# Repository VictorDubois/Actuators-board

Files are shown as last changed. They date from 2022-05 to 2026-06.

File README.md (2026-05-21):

Compact ESP32-based PCB, to control:
- 2 steppers
- 8 hobby servomotors (dedicated 6V DC-DC)
- AX12 Dynamixel numeric servomotors
- Addressable LEDs
- 2 vaccum sensors
- 4 generic GPIO connectors
- 3 generic I2C connectors
- 2 Krabi-Bus (12V/12V power/24V power/CAN)

[The code is available here](https://github.com/VictorDubois/ActuatorBoardCode)

[Click for online viewer
Capture d’écran du 2026-05-21 20-24-05
Capture d’écran du 2026-05-21 20-24-27
](https://kicanvas.org/?repo=https%3A%2F%2Fgithub.com%2FVictorDubois%2FActuators-board)

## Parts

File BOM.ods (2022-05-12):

> C1, C2 | 100nF | Capacitor_SMD:C_0805_2012Metric | ~ | 2 | 1.38
C4 | C | Capacitor_SMD:C_0805_2012Metric | ~ | 1 | 1.38
D1 | 13V | Diode_SMD:D_1206_3216Metric | ~ | 1 | 1.41
> D2, D3, D5, D30 | D_Zener | Diode_SMD:D_1206_3216Metric | ~ | 4 | 2/3 => 1.55 | D5/30 =>1,46
> D4, D6, D7, D25, D26, D31 | D | Diode_SMD:D_1206_3216Metric | ~ | 6 | 1.42
> D8-D24, D32, D33 | D_Zener_Small | Diode_SMD:D_1206_3216Metric | ~ | 19 | 1.39
> D27-D29 | LED_Small | LED_SMD:LED_0805_2012Metric | ~ | 3 | TOP
> Q1-Q4 | DMN2011UTS | Package_SO:TSSOP-8_4.4x3mm_P0.65mm | https://docs.rs-online.com/3df4/0900766b816b6b93.pdf | 4 | 1.44
> Q5, Q6 | DMP2040USD | Package_SO:SO-8_3.9x4.9mm_P1.27mm | https://docs.rs-online.com/a60c/0900766b816b6bbd.pdf | 2 | 1.43
> R1, R6 | 22kR | Resistor_SMD:R_0603_1608Metric | ~ | 2 | 1.54
R8 | 680R | Resistor_SMD:R_0603_1608Metric | ~ | 1 | 1.52
> R2-R5, R7, R9, R17-R20 | 220R | Resistor_SMD:R_0603_1608Metric | ~ | 10 | 1.40 | R2/R7 => 1.47 (2.2k)
R11 | open | Resistor_SMD:R_0603_1608Metric | ~ | 1
> R10, R12 | 0R | Resistor_SMD:R_0603_1608Metric | ~ | 2 | 1.45
> U1, U2 | XGZP6897D_differential_pressure_sensor | LibraryVictor:SOIC-8_7.5x5.85mm_P1.27mm |  | 2

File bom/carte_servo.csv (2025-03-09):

Reference | Value | LCSC# | Qty | Footprint | Datasheet | DNP
C1,C2,C7,C8,C10,C12,C23,C28,C29,C35 | 100nF | C14663 | 10 | Capacitor_SMD:C_0603_1608Metric | -- mixed values --
C3,C26,C27 | C_Polarized | C398835 | 3 | Capacitor_THT:CP_Radial_D10.0mm_P5.00mm | ~
C4,C9,C19,C20,C21,C22,C31,C32 | 10uF | C1713 | 8 | Capacitor_SMD:C_0805_2012Metric | ~
C5 | 1µF | C15849 | 1 | Capacitor_SMD:C_0603_1608Metric | ~
C6,C11 | 4.7µF | C1705 | 2 | Capacitor_SMD:C_0603_1608Metric | ~
C13 | 2.2uF | C19110 | 1 | Capacitor_SMD:C_0805_2012Metric | ~
C14 | 470nF | C7503496 | 1 | Capacitor_SMD:C_0603_1608Metric | ~
C15 | 68pF | C62782 | 1 | Capacitor_SMD:C_0603_1608Metric | ~
C16,C17,C30 | 47uF | C5440143 | 3 | Capacitor_SMD:C_1210_3225Metric | ~
C18 | 10nF | C57112 | 1 | Capacitor_SMD:C_0603_1608Metric | ~
C24,C25 | 22uF | C5674 | 2 | LED_SMD:LED_0805_2012Metric | ~
C33 | 470µF | C106619 | 1 | Capacitor_THT:CP_Radial_D7.5mm_P2.50mm | ~
C34 | C_Small | ? | 1 | Capacitor_SMD:C_0805_2012Metric | ~
D1,D8 | 13V | C173428 | 2 | Diode_SMD:D_SOD-123 | ~
D2,D3 | ESD321 | C3008120 | 2 | Diode_SMD:D_SOD-523 | https://www.mouser.fr/ProductDetail/Texas-Instruments/ESD321DYAR?qs=rQFj71Wb1eXoYwRMra0IYA%3D%3D
D4,D27 | LED_G | C965815 | 2 | LED_SMD:LED_0805_2012Metric | ~
D5,D6,D7,D13,D21,D22,D23,D24,D25,D26,D30,D32,D33,D34,D35,D36,D37,D38,D41,D48 | D_Zener_Small | C908230 | 20 | Diode_SMD:D_SOD-123 | ~
D29 | LED_R | C965812 | 1 | LED_SMD:LED_0805_2012Metric | ~
F1,F2 | Fuse 4A | C27515 | 2 | Fuse:Fuse_Littelfuse-NANO2-451_453 | ~
J1,J3 | Conn_01x04_Pin | C595709 | 2 | Connector_JST:JST_XH_B4B-XH-A_1x04_P2.50mm_Vertical | Stepper
J2,J22 | Conn_02x04_Top_Bottom | C277661 | 2 | Connector_Molex:Molex_Micro-Fit_3.0_43045-0812_2x04_P3.00mm_Vertical | ~
J4,J26,J27,J28 | Conn_01x03 | C144394 | 4 | Connector_JST:JST_XH_B3B-XH-A_1x03_P2.50mm_Vertical | ~
J5,J6,J7,J8,J9,J10,J18,J19 | Conn_01x03_Male | C2937625 | 8 | Connector_PinHeader_2.54mm:PinHeader_1x03_P2.54mm_Vertical | ~
J11 | Transistor_2 | C158012 | 1 | Connector_JST:JST_XH_B2B-XH-A_1x02_P2.50mm_Vertical | ~
J12 | Transistor_1 | C158012 | 1 | Connector_JST:JST_XH_B2B-XH-A_1x02_P2.50mm_Vertical | ~
J13 | Transistor_4 | C158012 | 1 | Connector_JST:JST_XH_B2B-XH-A_1x02_P2.50mm_Vertical | ~
J14 | Transistor_.3 | C158012 | 1 | Connector_JST:JST_XH_B2B-XH-A_1x02_P2.50mm_Vertical | ~
J16,J17,J23 | Conn_01x05 | C495550 | 3 | Connector_JST:JST_XH_B5B-XH-A_1x05_P2.50mm_Vertical | ~
J24 | Conn_LEDs | C144394 | 1 | Connector_JST:JST_XH_B3B-XH-A_1x03_P2.50mm_Vertical | ~
J25,J29 | Conn_AX12 | C144394 | 2 | Connector_JST:JST_XH_B3B-XH-A_1x03_P2.50mm_Vertical | ~
L1 | XAL6030-122MEC | C19191689 | 1 | XAL6030-122MEC:IND_XAL6030-122MEC | https://www.mouser.fr/ProductDetail/Coilcraft/XAL6030-122MEC?qs=zCSbvcPd3pa9JIn1HYfyrA%3D%3D
L2 | IHLP2525CZER3R3M11 | C845025 | 1 | INDPM6965X300N | https://datasheet.datasheetarchive.com/originals/distributors/Datasheets-DGA11/2253392.pdf
P1 | USB_C_Plug_USB2.0 | C963216 | 1 | USBC:G-Switch GT-USB-7047A | https://www.lcsc.com/product-detail/USB-Connectors_G-Switch-GT-USB-7047A_C963216.html
Q1,Q2,Q3,Q4,Q6 | DMN2011UTS | C5245271 | 5 | Package_SO:TSSOP-8_4.4x3mm_P0.65mm | https://docs.rs-online.com/3df4/0900766b816b6b93.pdf
Q7 | CSD17307Q5A | C22367097 | 1 | Package_TO_SOT_SMD:TDSON-8-1 | http://www.ti.com/lit/gpn/csd17307q5a
Q8 | CSD17579Q5A | C2760461 | 1 | Package_TO_SOT_SMD:TDSON-8-1 | http://www.ti.com/lit/gpn/csd17579q5a
R1 | 1.74k | C2930053 | 1 | Capacitor_SMD:C_0603_1608Metric | ~
R2,R17,R18,R19,R20 | 220R | C2907127 | 5 | Resistor_SMD:R_0603_1608Metric | ~
R3,R4 | 2kR | C2907137 | 2 | Resistor_SMD:R_0603_1608Metric | ~
R5,R27,R29 | 5.11kR | C2933233 | 3 | Resistor_SMD:R_0603_1608Metric | ~
R6,R7,R12,R13,R14 | NC |  | 5 | Resistor_SMD:R_0603_1608Metric | ~
R8,R31 | 52.3kR | C23198 | 2 | Resistor_SMD:R_0603_1608Metric | ~
R9,R22,R23,R24,R26,R35,R36 | 10kR | C2930027 | 7 | Resistor_SMD:R_0603_1608Metric | ~
R10,R11,R15,R16,R37 | 0R | C21189 | 5 | Resistor_SMD:R_0603_1608Metric | ~
R21 | 510R | C2907179 | 1 | Resistor_SMD:R_0805_2012Metric | ~
R25,R30 | 22kR | C2907128 | 2 | Resistor_SMD:R_0603_1608Metric | ~
R28 | 1MR | C22935 | 1 | Resistor_SMD:R_0603_1608Metric | ~
R32 | 88.7k | C2999456 | 1 | Capacitor_SMD:C_0603_1608Metric | ~
R33 | 9.76k | C2933269 | 1 | Capacitor_SMD:C_0603_1608Metric | ~
R34 | 56.2k | C2930117 | 1 | Capacitor_SMD:C_0603_1608Metric | ~
R38,R39 | 1kR | C2907113 | 2 | Resistor_SMD:R_0603_1608Metric | ~
R40,R41,R42,R43,R44,R45,R46,R47 | R_Small |  | 8 | Resistor_SMD:R_0603_1608Metric | ~
SW2 | SW_Push | C2888419 | 1 | button:BZCN TSA007A1518B03 | https://www.lcsc.com/product-detail/Tactile-Switches_BZCN-TSA007A1518B03_C2888419.html
U1,U2 | XGZP6897D_differential_pressure_sensor |  | 2 | LibraryVictor:SOIC-8_7.5x5.85mm_P1.27mm
U3,U4 | TMC2208_SILENTSTEPSTICK |  | 2 | TMC2208_SILENTSTEPSTICK:MODULE_TMC2208_SILENTSTEPSTICK
U5 | 74LVC2G241 | C10430 | 1 | Package_SO:VSSOP-8_2.4x2.1mm_P0.5mm | http://www.ti.com/lit/sg/scyt129e/scyt129e.pdf
U6 | SN65HVD230 | C12084 | 1 | Package_SO:SOIC-8_3.9x4.9mm_P1.27mm | http://www.ti.com/lit/ds/symlink/sn65hvd230.pdf
U7 | LD1117S33TR_SOT223 | C20538890 | 1 | Package_TO_SOT_SMD:SOT-223-3_TabPin2 | http://www.st.com/st-web-ui/static/active/en/resource/technical/document/datasheet/CD00000544.pdf
U8 | ESP32-S3-WROOM-1 | C2913198 | 1 | PCM_Espressif:ESP32-S3-WROOM-1U | https://www.espressif.com/sites/default/files/documentation/esp32-s3-wroom-1_wroom-1u_datasheet_en.pdf
U9 | LM3150MH | C1519420 | 1 | Package_SO:HTSSOP-14-1EP_4.4x5mm_P0.65mm_EP3.4x5mm_Mask3x3.1mm | http://www.ti.com/lit/ds/symlink/lm3150.pdf
U10 | TPS563200 | C97253 | 1 | Package_TO_SOT_SMD:SOT-23-6 | http://www.ti.com/lit/ds/symlink/tps563200.pdf
U11 | PCF8574ATS | C2803277 | 1 | Package_SO:SSOP-20_4.4x6.5mm_P0.65mm | http://www.nxp.com/docs/en/data-sheet/PCF8574_PCF8574A.pdf

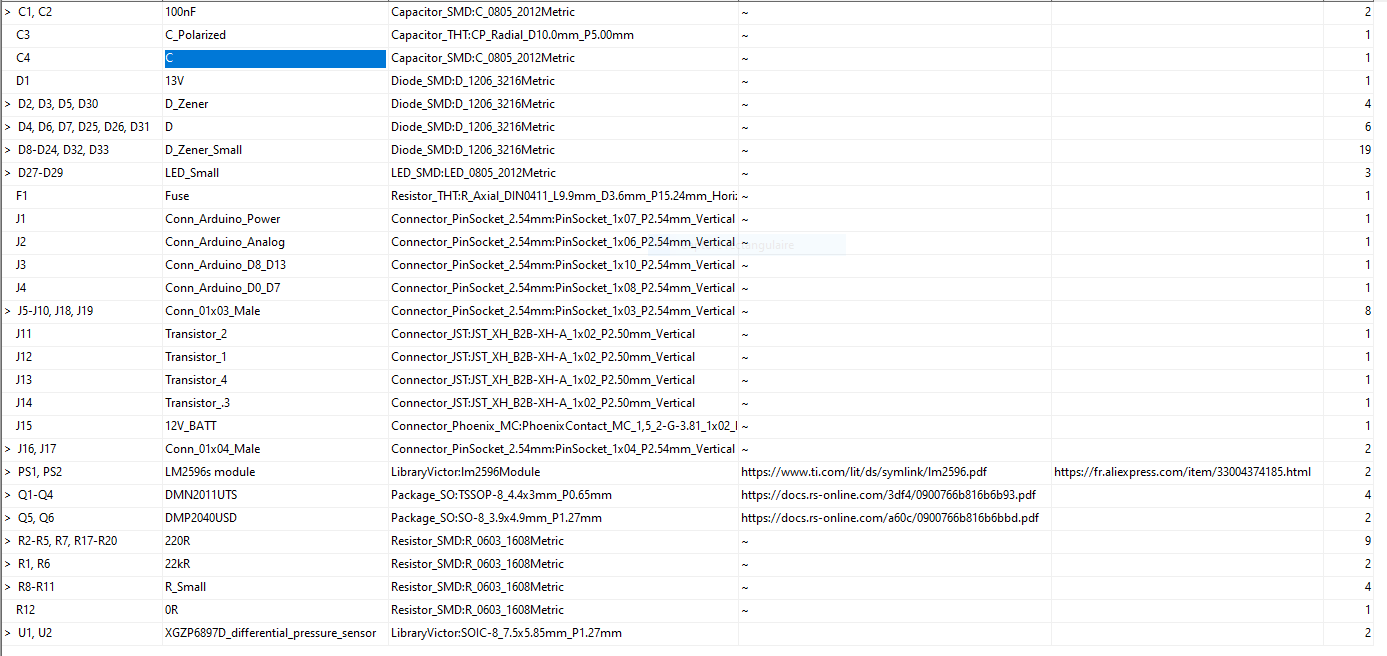
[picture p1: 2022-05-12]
BOM.PNG

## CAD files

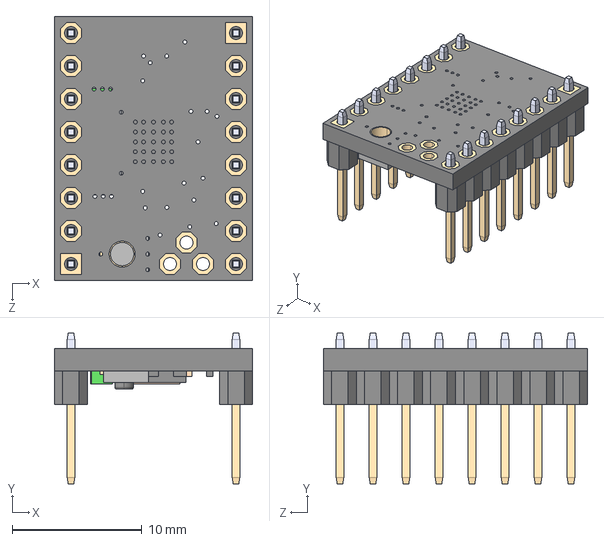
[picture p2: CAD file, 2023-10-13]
TMC2208_SILENTSTEPSTICK/TMC2208_SILENTSTEPSTICK.step
15.2 x 11.6 x 20.3 mm

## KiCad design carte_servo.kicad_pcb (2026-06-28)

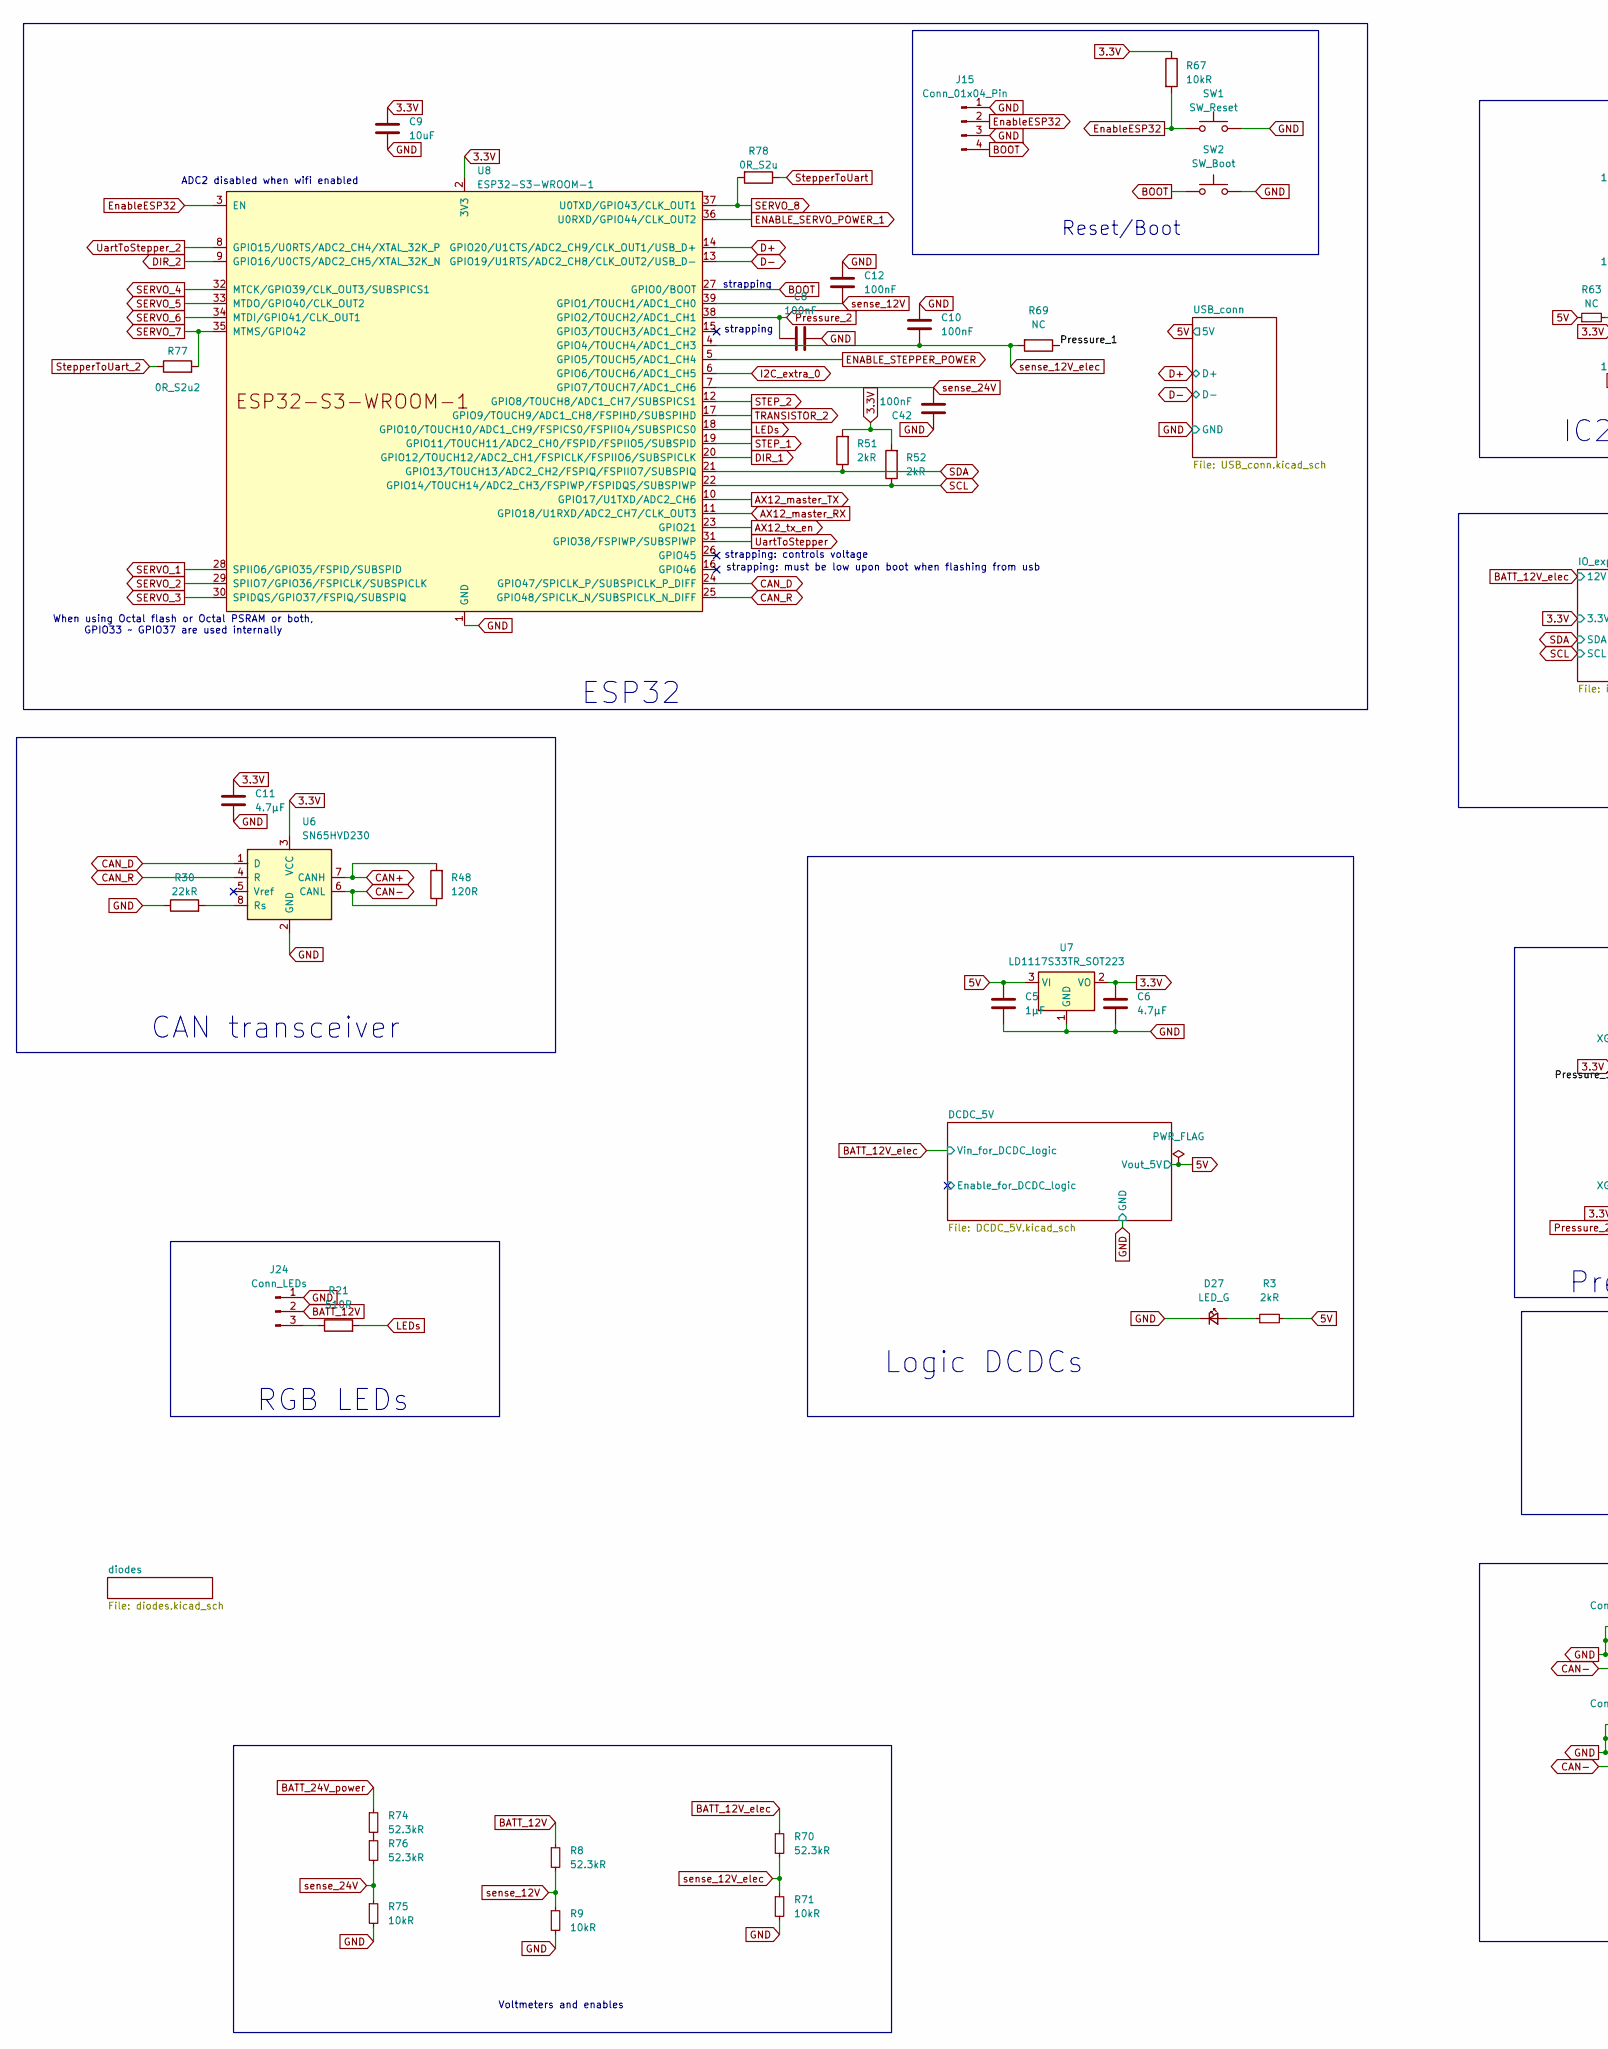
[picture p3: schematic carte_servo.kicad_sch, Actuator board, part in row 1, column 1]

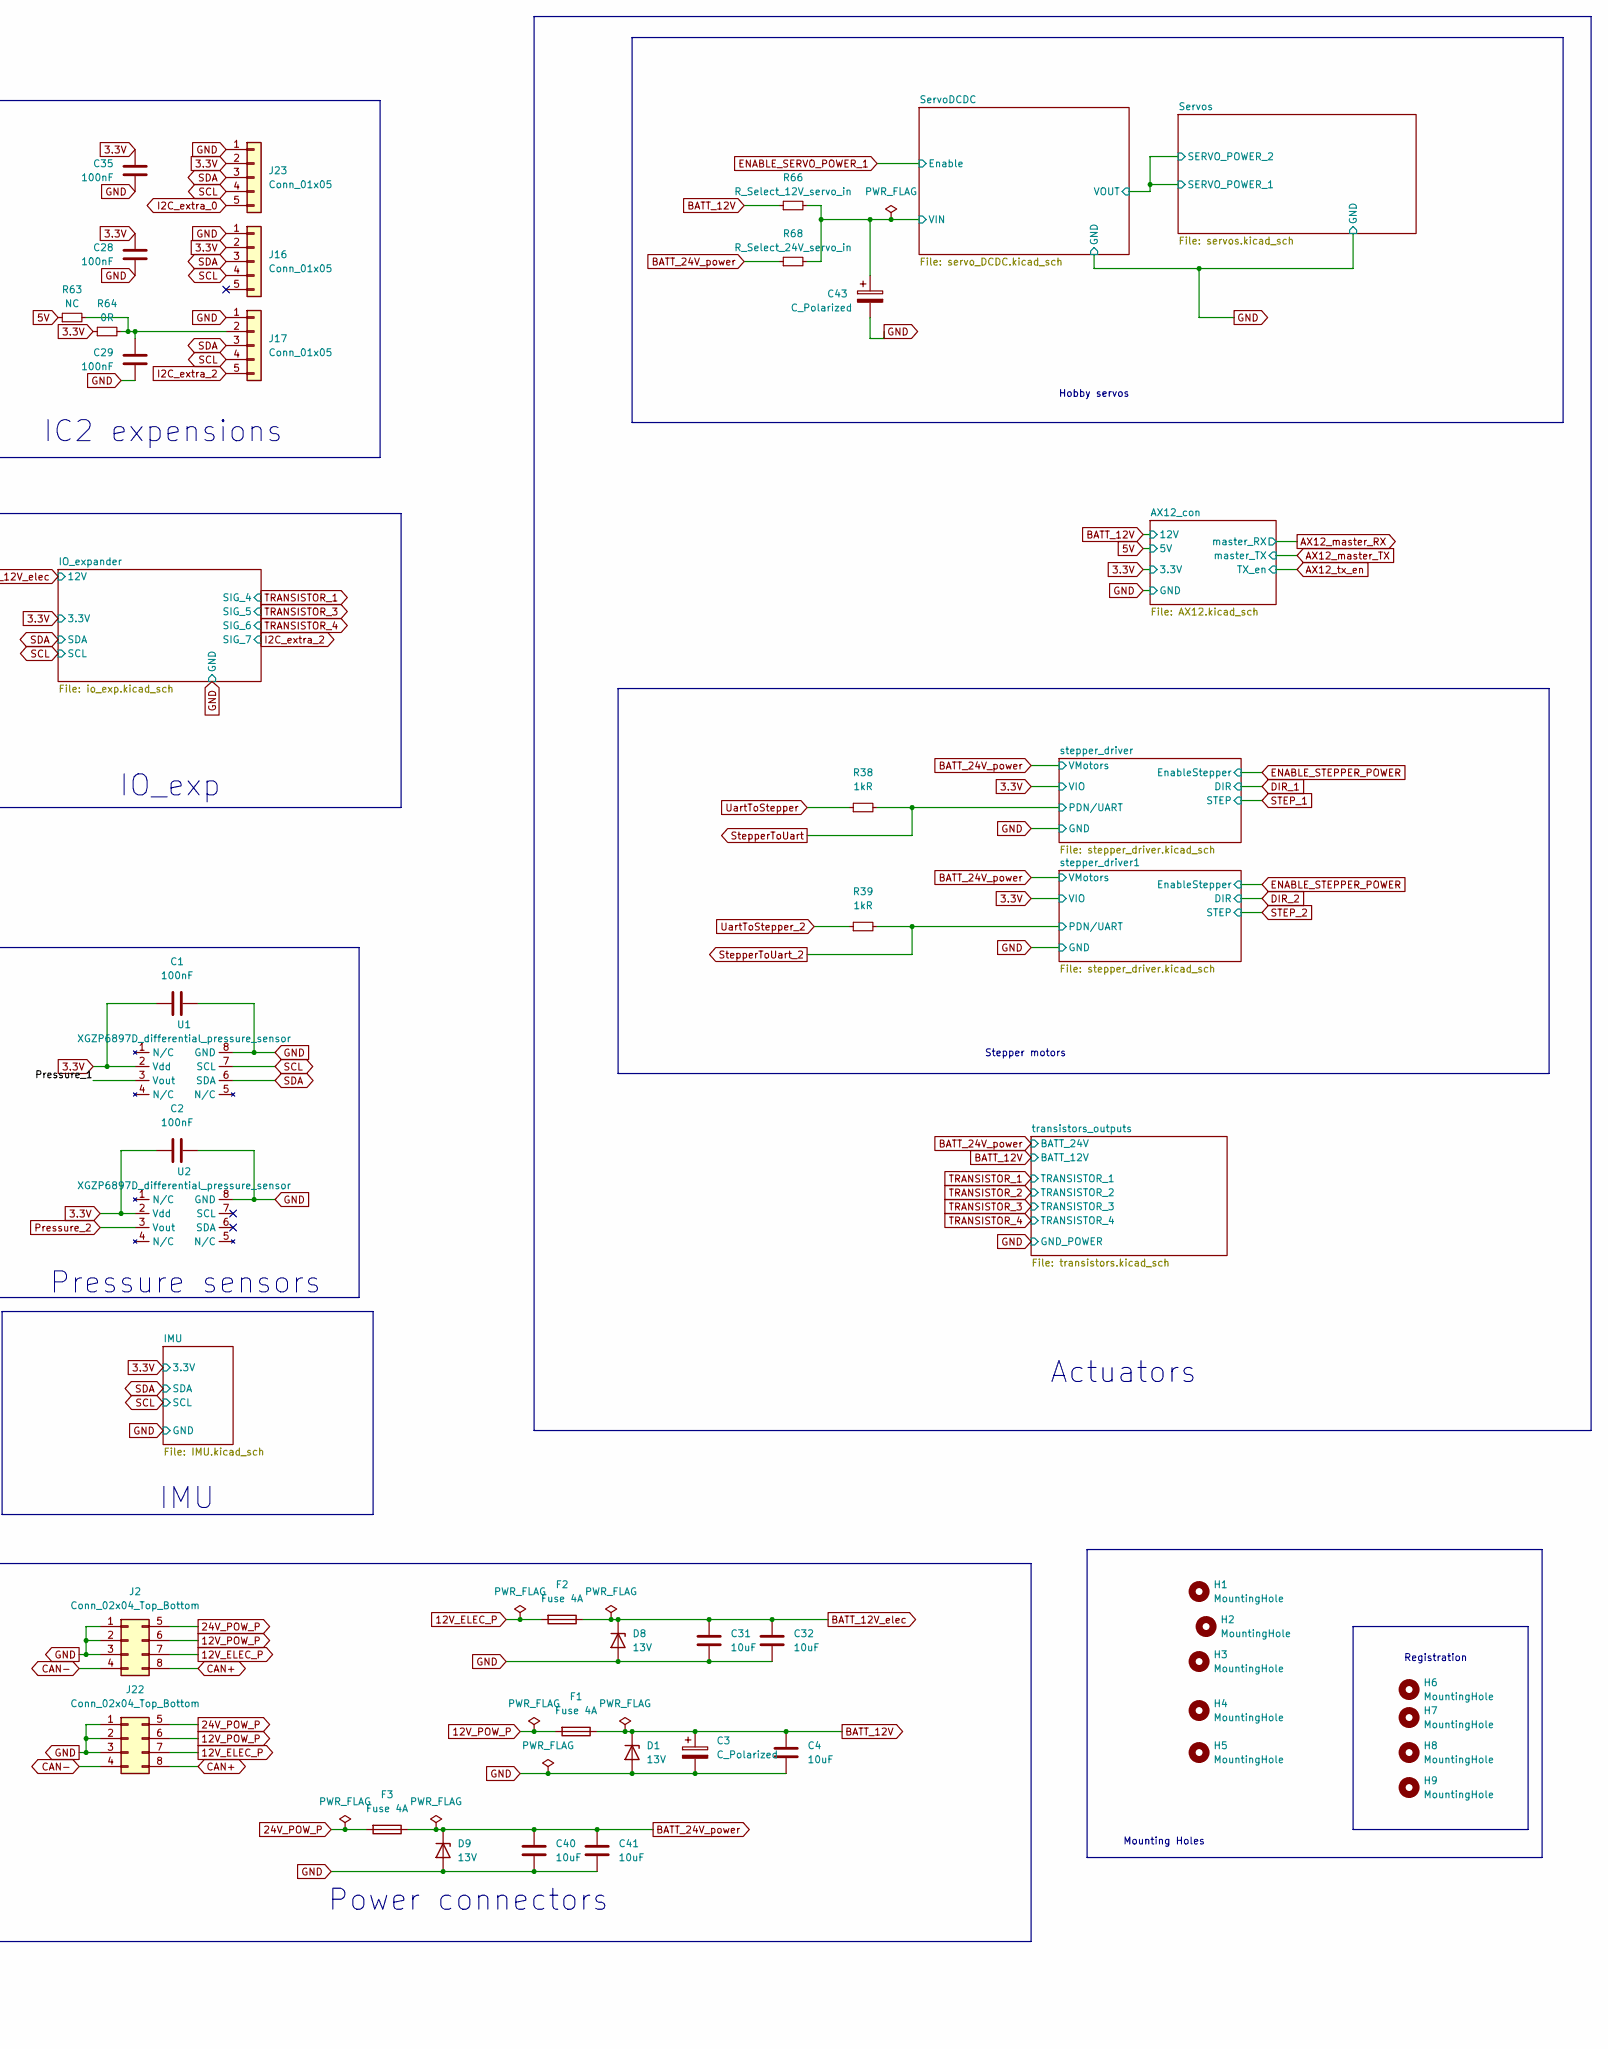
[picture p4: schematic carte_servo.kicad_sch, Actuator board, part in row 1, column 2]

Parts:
C1, C2, C8, C10, C12, C28, C29, C35, C42: 100nF; C_0603_1608Metric; LCSC# C14663
C3: C_Polarized; CP_Radial_D10.0mm_P5.00mm; LCSC# C398835
C4, C9, C31, C32, C40, C41: 10uF; C_0805_2012Metric; LCSC# C440198
C5: 1µF; C_0603_1608Metric; LCSC# C15849
C6, C11: 4.7µF; C_0603_1608Metric; LCSC# C1705
C43: C_Polarized; CP_Elec_10x10.5; LCSC# C233118
D1, D8, D9: 13V; D_SOD-123; LCSC# C173428
D27: LED_G; LED_0805_2012Metric; LCSC# C965815
F1, F2, F3: Fuse 4A; Fuse_Littelfuse-NANO2-451_453; LCSC# C27515
H1, H2, H3, H4, H5: MountingHole; MountingHole_3.2mm_M3
H6, H7: MountingHole; MountingHole_3mm
H8, H9: MountingHole; MountingHole_5mm
J2, J22: Conn_02x04_Top_Bottom; Molex_Micro-Fit_3.0_43045-0812_2x04_P3.00mm_Vertical; LCSC# C277661
J15: Conn_01x04_Pin; JST_PH_B4B-PH-K_1x04_P2.00mm_Vertical; LCSC# C595709
J16, J17, J23: Conn_01x05; JST_XH_B5B-XH-A_1x05_P2.50mm_Vertical; LCSC# C495550
J24: Conn_LEDs; JST_XH_B3B-XH-A_1x03_P2.50mm_Vertical; LCSC# C144394
R3, R51, R52: 2kR; R_0603_1608Metric; LCSC# C2907137
R8, R70, R74, R76: 52.3kR; R_0603_1608Metric; LCSC# C23198
R9, R67, R71, R75: 10kR; R_0603_1608Metric; LCSC# C2930027
R21: 510R; R_0805_2012Metric; LCSC# C2907179
R30: 22kR; R_0603_1608Metric; LCSC# C2907128
R38, R39: 1kR; R_0603_1608Metric; LCSC# C2907113
R48: 120R; R_0603_1608Metric; LCSC# C2907128
R63, R69: NC; R_0603_1608Metric
R64: 0R; R_0603_1608Metric; LCSC# C21189
R66: R_Select_12V_servo_in; R_1206_3216Metric; LCSC# C2907406
R68: R_Select_24V_servo_in; R_1206_3216Metric; LCSC# C2907406
R77: 0R_S2u2; R_0603_1608Metric; LCSC# C2907128
R78: 0R_S2u; R_0603_1608Metric; LCSC# C2907128
SW1: SW_Reset; BZCN TSA007A1518B03; LCSC# C2888419
SW2: SW_Boot; BZCN TSA007A1518B03; LCSC# C2888419
U1, U2: XGZP6897D_differential_pressure_sensor; SOIC-8_7.5x5.85mm_P1.27mm
U6: SN65HVD230; SOIC-8_3.9x4.9mm_P1.27mm; LCSC# C12084
U7: LD1117S33TR_SOT223; SOT-223-3_TabPin2; LCSC# C20538890
U8: ESP32-S3-WROOM-1; ESP32-S3-WROOM-1U; LCSC# C2980297

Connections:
3.3V: C1.2, C2.2, C6.1, C9.1, C11.1, C28.1, C35.1, J16.2, J23.2, R51.2, R52.2, R64.1, R67.1, U1.2 (Vdd), U2.2 (Vdd), U6.3 (VCC), U7.2 (VO), U8.2 (3V3); also elsewhere on the board
5V: C5.1, R3.2, R63.1, U7.3 (VI); also elsewhere on the board
12V_ELEC_P: F2.2, J2.7, J22.7
12V_POW_P: F1.2, J2.6, J22.6
24V_POW_P: F3.2, J2.5, J22.5
/Pressure_1: R69.1, U1.3 (Vout)
/ServoDCDC/VIN: C43.1, R66.2, R68.2; also elsewhere on the board
AX12_master_RX: U8.11 (GPIO18/U1RXD/ADC2_CH7/CLK_OUT3); also elsewhere on the board
AX12_master_TX: U8.10 (GPIO17/U1TXD/ADC2_CH6); also elsewhere on the board
AX12_tx_en: U8.23 (GPIO21); also elsewhere on the board
BATT_12V: C3.1, C4.1, D1.1 (K), F1.1, J24.2, R8.1, R66.1; also elsewhere on the board
BATT_12V_elec: C31.1, C32.1, D8.1 (K), F2.1, R70.1; also elsewhere on the board
BATT_24V_power: C40.1, C41.1, D9.1 (K), F3.1, R68.1, R74.1; also elsewhere on the board
BOOT: J15.4, SW2.1, U8.27 (GPIO0/BOOT)
CAN+: J2.8, J22.8, R48.2, U6.7 (CANH)
CAN-: J2.4, J22.4, R48.1, U6.6 (CANL)
CAN_D: U6.1 (D), U8.24 (GPIO47/SPICLK_P/SUBSPICLK_P_DIFF)
CAN_R: U6.4 (R), U8.25 (GPIO48/SPICLK_N/SUBSPICLK_N_DIFF)
D+: U8.14 (GPIO20/U1CTS/ADC2_CH9/CLK_OUT1/USB_D+); also elsewhere on the board
D-: U8.13 (GPIO19/U1RTS/ADC2_CH8/CLK_OUT2/USB_D-); also elsewhere on the board
DIR_1: U8.20 (GPIO12/TOUCH12/ADC2_CH1/FSPICLK/FSPIIO6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); also elsewhere on the board
DIR_2: U8.9 (GPIO16/U0CTS/ADC2_CH5/XTAL_32K_N); also elsewhere on the board
ENABLE_SERVO_POWER_1: U8.36 (U0RXD/GPIO44/CLK_OUT2); also elsewhere on the board
ENABLE_STEPPER_POWER: U8.5 (GPIO5/TOUCH5/ADC1_CH4); also elsewhere on the board
EnableESP32: J15.2, R67.2, SW1.1, U8.3 (EN)
GND: C1.1, C2.1, C3.2, C4.2, C5.2, C6.2, C8.2, C9.2, C10.1, C11.2, C12.1, C28.2, C29.2, C31.2, C32.2, C35.2, C40.2, C41.2, C42.1, C43.2, D1.2 (A), D8.2 (A), D9.2 (A), D27.1 (K), J2.1, J2.2, J2.3, J15.1, J15.3, J16.1, J17.1, J22.1, J22.2, J22.3, J23.1, J24.1, R9.2, R30.1, R71.2, R75.2, SW1.2, SW2.2, U1.8 (GND), U2.8 (GND), U6.2 (GND), U7.1 (GND), U8.1 (GND), U8.40 (GND), U8.41 (GND); also elsewhere on the board
I2C_extra_0: J23.5, U8.6 (GPIO6/TOUCH6/ADC1_CH5)
I2C_extra_2: J17.5; also elsewhere on the board
LEDs: R21.2, U8.18 (GPIO10/TOUCH10/ADC1_CH9/FSPICS0/FSPIIO4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); also elsewhere on the board
unnamed: D27.2 (A), R3.1
unnamed: C29.1, J17.2, R63.2, R64.2
unnamed: J24.3, R21.1
unnamed: R74.2, R76.1
unnamed: R30.2, U6.8 (Rs)
Pressure_2: C8.1, U2.3 (Vout), U8.38 (GPIO2/TOUCH2/ADC1_CH1)
SCL: J16.4, J17.4, J23.4, R52.1, U1.7 (SCL), U8.22 (GPIO14/TOUCH14/ADC2_CH3/FSPIWP/FSPIDQS/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); also elsewhere on the board
SDA: J16.3, J17.3, J23.3, R51.1, U1.6 (SDA), U8.21 (GPIO13/TOUCH13/ADC2_CH2/FSPIQ/FSPIIO7/S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); also elsewhere on the board
SERVO_1: U8.28 (SPIIO6/GPIO35/FSPID/SUBSPID); also elsewhere on the board
SERVO_2: U8.29 (SPIIO7/GPIO36/FSPICLK/SUBSPICLK); also elsewhere on the board
SERVO_3: U8.30 (SPIDQS/GPIO37/FSPIQ/SUBSPIQ); also elsewhere on the board
SERVO_4: U8.32 (MTCK/GPIO39/CLK_OUT3/SUBSPICS1); also elsewhere on the board
SERVO_5: U8.33 (MTDO/GPIO40/CLK_OUT2); also elsewhere on the board
SERVO_6: U8.34 (MTDI/GPIO41/CLK_OUT1); also elsewhere on the board
SERVO_7: R77.2, U8.35 (MTMS/GPIO42); also elsewhere on the board
SERVO_8: R78.2, U8.37 (U0TXD/GPIO43/CLK_OUT1); also elsewhere on the board
STEP_1: U8.19 (GPIO11/TOUCH11/ADC2_CH0/FSPID/FSPIIO5/S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); also elsewhere on the board
STEP_2: U8.12 (GPIO8/TOUCH8/ADC1_CH7/SUBSPICS1); also elsewhere on the board
StepperToUart: R38.2, R78.1; also elsewhere on the board
StepperToUart_2: R39.2, R77.1; also elsewhere on the board
TRANSISTOR_2: U8.17 (GPIO9/TOUCH9/ADC1_CH8/FSPIHD/SUBSPIHD); also elsewhere on the board
UartToStepper: R38.1, U8.31 (GPIO38/FSPIWP/SUBSPIWP)
UartToStepper_2: R39.1, U8.8 (GPIO15/U0RTS/ADC2_CH4/XTAL_32K_P)
sense_12V: C12.2, R8.2, R9.1, U8.39 (GPIO1/TOUCH1/ADC1_CH0)
sense_12V_elec: C10.2, R69.2, R70.2, R71.1, U8.4 (GPIO4/TOUCH4/ADC1_CH3)
sense_24V: C42.2, R75.1, R76.2, U8.7 (GPIO7/TOUCH7/ADC1_CH6)

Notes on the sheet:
IMU
IO_exp
ADC2 disabled when wifi enabled
Hobby servos
strapping: must be low upon boot when flashing from usb
Voltmeters and enables
When using Octal flash or Octal PSRAM or both, GPIO33 ~ GPIO37 are used internally
Actuators
strapping
Registration
Power connectors
Stepper motors
strapping: controls voltage
IC2 expensions
ESP32
CAN transceiver
Logic DCDCs
RGB LEDs
Pressure sensors
Reset/Boot
Mounting Holes

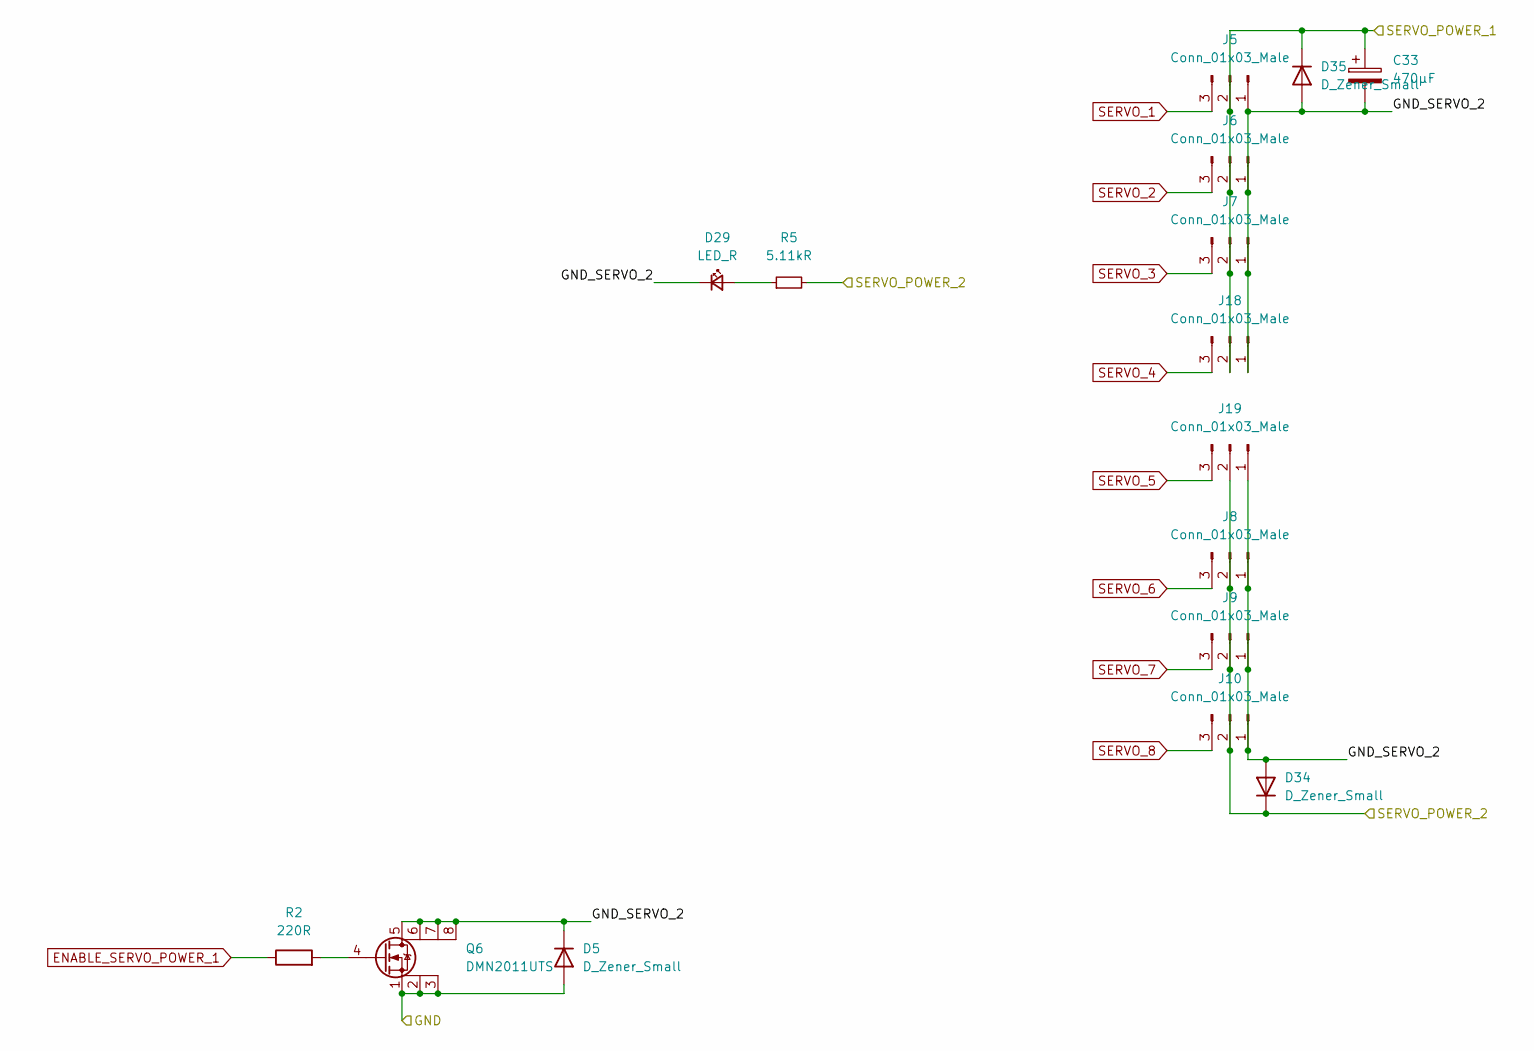
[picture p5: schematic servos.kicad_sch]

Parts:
C33: 470µF; CP_Radial_D7.5mm_P2.50mm; LCSC# C106619
D5, D34, D35: D_Zener_Small; D_SOD-123; LCSC# C908230
D29: LED_R; LED_0805_2012Metric; LCSC# C965812
J5, J6, J7, J8, J9, J10, J18, J19: Conn_01x03_Male; PinHeader_1x03_P2.54mm_Vertical; LCSC# C2937625
Q6: DMN2011UTS; TSSOP-8_4.4x3mm_P0.65mm; LCSC# C5245271
R2: 220R; R_0603_1608Metric; LCSC# C2907127
R5: 5.11kR; R_0603_1608Metric; LCSC# C2933233

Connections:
/ServoDCDC/VOUT: C33.1, D34.1 (K), D35.1 (K), J5.2, J6.2, J7.2, J8.2, J9.2, J10.2, J18.2, J19.2, R5.2; also elsewhere on the board
/Servos/GND_SERVO_2: C33.2, D5.1 (K), D29.1 (K), D34.2 (A), D35.2 (A), J5.1, J6.1, J7.1, J8.1, J9.1, J10.1, J18.1, J19.1, Q6.5 (D), Q6.6 (D), Q6.7 (D), Q6.8 (D)
ENABLE_SERVO_POWER_1: R2.1; also elsewhere on the board
GND: D5.2 (A), Q6.1 (S), Q6.2 (S), Q6.3 (S); also elsewhere on the board
unnamed: D29.2 (A), R5.1
unnamed: Q6.4 (G), R2.2
SERVO_1: J5.3; also elsewhere on the board
SERVO_2: J6.3; also elsewhere on the board
SERVO_3: J7.3; also elsewhere on the board
SERVO_4: J18.3; also elsewhere on the board
SERVO_5: J19.3; also elsewhere on the board
SERVO_6: J8.3; also elsewhere on the board
SERVO_7: J9.3; also elsewhere on the board
SERVO_8: J10.3; also elsewhere on the board

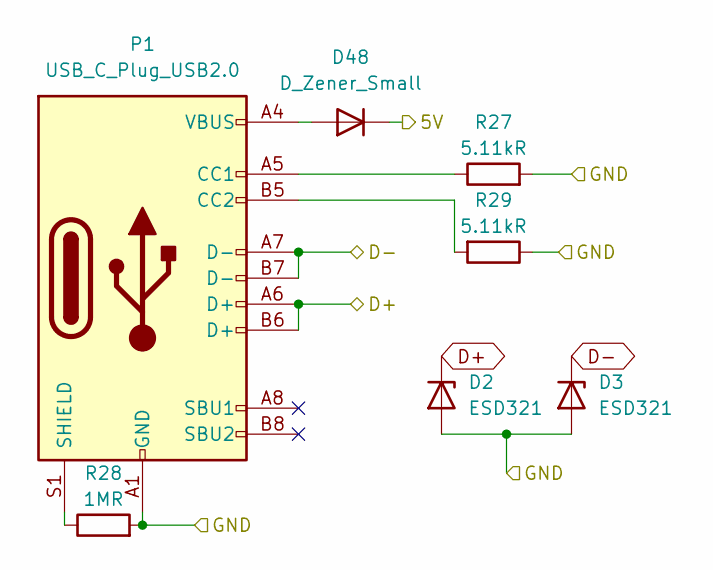
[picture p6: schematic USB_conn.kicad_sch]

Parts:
D2, D3: ESD321; D_SOD-523; LCSC# C3008120
D48: D_Zener_Small; D_SOD-123; LCSC# C908230
P1: USB_C_Plug_USB2.0; G-Switch GT-USB-7047A; LCSC# C963216
R27, R29: 5.11kR; R_0603_1608Metric; LCSC# C2933233
R28: 1MR; R_0603_1608Metric; LCSC# C22935

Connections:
5V: D48.1 (K); also elsewhere on the board
D+: D2.1 (K), P1.A6 (D+), P1.B6 (D+); also elsewhere on the board
D-: D3.1 (K), P1.A7 (D-), P1.B7 (D-); also elsewhere on the board
GND: D2.2 (A), D3.2 (A), P1.A1 (GND), P1.A12 (GND), P1.B1 (GND), P1.B12 (GND), R27.2, R28.2, R29.1; also elsewhere on the board
unnamed: D48.2 (A), P1.A4 (VBUS), P1.A9 (VBUS), P1.B4 (VBUS), P1.B9 (VBUS)
unnamed: P1.A5 (CC1), R27.1
unnamed: P1.B5 (CC2), R29.2
unnamed: P1.S1 (SHIELD), R28.1

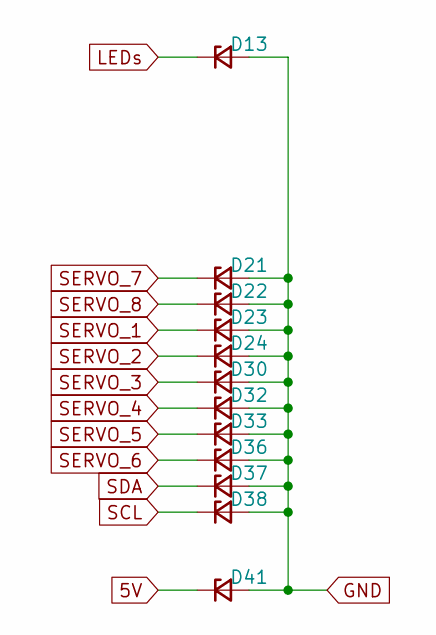
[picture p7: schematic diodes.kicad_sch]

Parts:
D13, D21, D22, D23, D24, D30, D32, D33, D36, D37, D38, D41: D_Zener_Small; D_SOD-123; LCSC# C908230

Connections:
5V: D41.1 (K); also elsewhere on the board
GND: D13.2 (A), D21.2 (A), D22.2 (A), D23.2 (A), D24.2 (A), D30.2 (A), D32.2 (A), D33.2 (A), D36.2 (A), D37.2 (A), D38.2 (A), D41.2 (A); also elsewhere on the board
LEDs: D13.1 (K); also elsewhere on the board
SCL: D38.1 (K); also elsewhere on the board
SDA: D37.1 (K); also elsewhere on the board
SERVO_1: D23.1 (K); also elsewhere on the board
SERVO_2: D24.1 (K); also elsewhere on the board
SERVO_3: D30.1 (K); also elsewhere on the board
SERVO_4: D32.1 (K); also elsewhere on the board
SERVO_5: D33.1 (K); also elsewhere on the board
SERVO_6: D36.1 (K); also elsewhere on the board
SERVO_7: D21.1 (K); also elsewhere on the board
SERVO_8: D22.1 (K); also elsewhere on the board

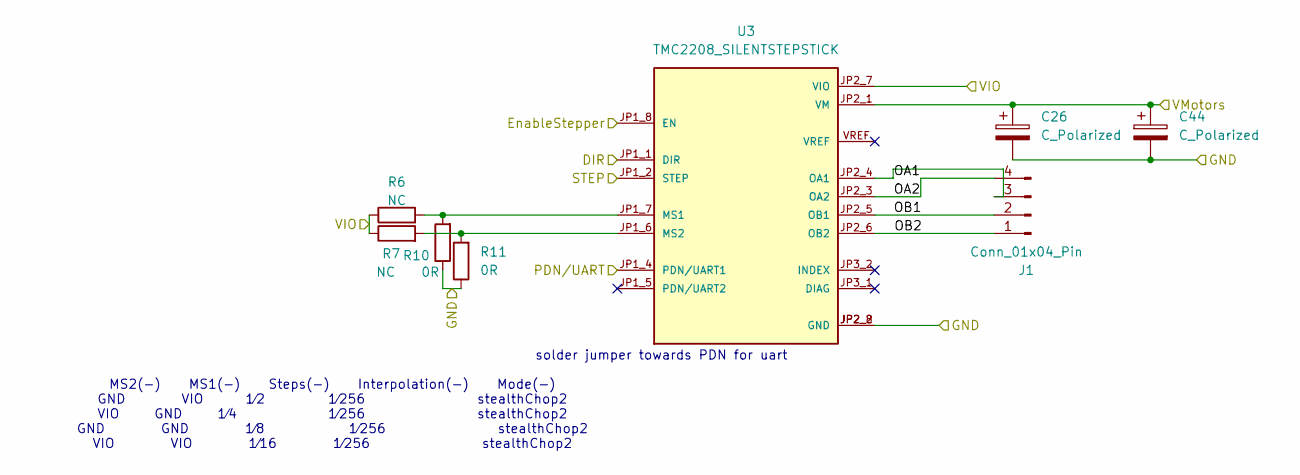
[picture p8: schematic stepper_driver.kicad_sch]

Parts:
C26: C_Polarized; CP_Radial_D10.0mm_P5.00mm; LCSC# C398835
C44: C_Polarized; CP_Elec_10x10.5; LCSC# C398835
J1: Conn_01x04_Pin; JST_XH_B4B-XH-A_1x04_P2.50mm_Vertical; LCSC# C595709
R6, R7: NC; R_0603_1608Metric
R10, R11: 0R; R_0603_1608Metric; LCSC# C21189
U3: TMC2208_SILENTSTEPSTICK; MODULE_TMC2208_SILENTSTEPSTICK

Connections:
3.3V: R6.1, R7.1, U3.JP2_7 (VIO); also elsewhere on the board
/stepper_driver/OA1: J1.3, U3.JP2_4 (OA1)
/stepper_driver/OA2: J1.4, U3.JP2_3 (OA2)
/stepper_driver/OB1: J1.2, U3.JP2_5 (OB1)
/stepper_driver/OB2: J1.1, U3.JP2_6 (OB2)
BATT_24V_power: C26.1, C44.1, U3.JP2_1 (VM); also elsewhere on the board
DIR_1: U3.JP1_1 (DIR); also elsewhere on the board
ENABLE_STEPPER_POWER: U3.JP1_8 (EN); also elsewhere on the board
GND: C26.2, C44.2, R10.1, R11.1, U3.JP2_2 (GND), U3.JP2_8 (GND); also elsewhere on the board
unnamed: R6.2, R10.2, U3.JP1_7 (MS1)
unnamed: R7.2, R11.2, U3.JP1_6 (MS2)
STEP_1: U3.JP1_2 (STEP); also elsewhere on the board
StepperToUart: U3.JP1_4 (PDN/UART1); also elsewhere on the board

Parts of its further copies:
C27: C_Polarized; CP_Radial_D10.0mm_P5.00mm; LCSC# C398835
C45: C_Polarized; CP_Elec_10x10.5; LCSC# C398835
J3: Conn_01x04_Pin; JST_XH_B4B-XH-A_1x04_P2.50mm_Vertical; LCSC# C595709
R13, R14: NC; R_0603_1608Metric
R15, R16: 0R; R_0603_1608Metric; LCSC# C21189
U4: TMC2208_SILENTSTEPSTICK; MODULE_TMC2208_SILENTSTEPSTICK

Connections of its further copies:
3.3V: R13.1, R14.1, U4.JP2_7 (VIO); also elsewhere on the board
/stepper_driver1/OA1: J3.3, U4.JP2_4 (OA1)
/stepper_driver1/OA2: J3.4, U4.JP2_3 (OA2)
/stepper_driver1/OB1: J3.2, U4.JP2_5 (OB1)
/stepper_driver1/OB2: J3.1, U4.JP2_6 (OB2)
BATT_24V_power: C27.1, C45.1, U4.JP2_1 (VM); also elsewhere on the board
DIR_2: U4.JP1_1 (DIR); also elsewhere on the board
ENABLE_STEPPER_POWER: U4.JP1_8 (EN); also elsewhere on the board
GND: C27.2, C45.2, R15.1, R16.1, U4.JP2_2 (GND), U4.JP2_8 (GND); also elsewhere on the board
unnamed: R13.2, R15.2, U4.JP1_7 (MS1)
unnamed: R14.2, R16.2, U4.JP1_6 (MS2)
STEP_2: U4.JP1_2 (STEP); also elsewhere on the board
StepperToUart_2: U4.JP1_4 (PDN/UART1); also elsewhere on the board

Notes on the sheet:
solder jumper towards PDN for uart
MS2(-) MS1(-) Steps(-) Interpolation(-) Mode(-) GND VIO 1⁄2 1⁄256 stealthChop2 VIO GND 1⁄4 1⁄256 stealthChop2 GND GND 1⁄8 1⁄256 stealthChop2 VIO VIO 1⁄16 1⁄256 stealthChop2

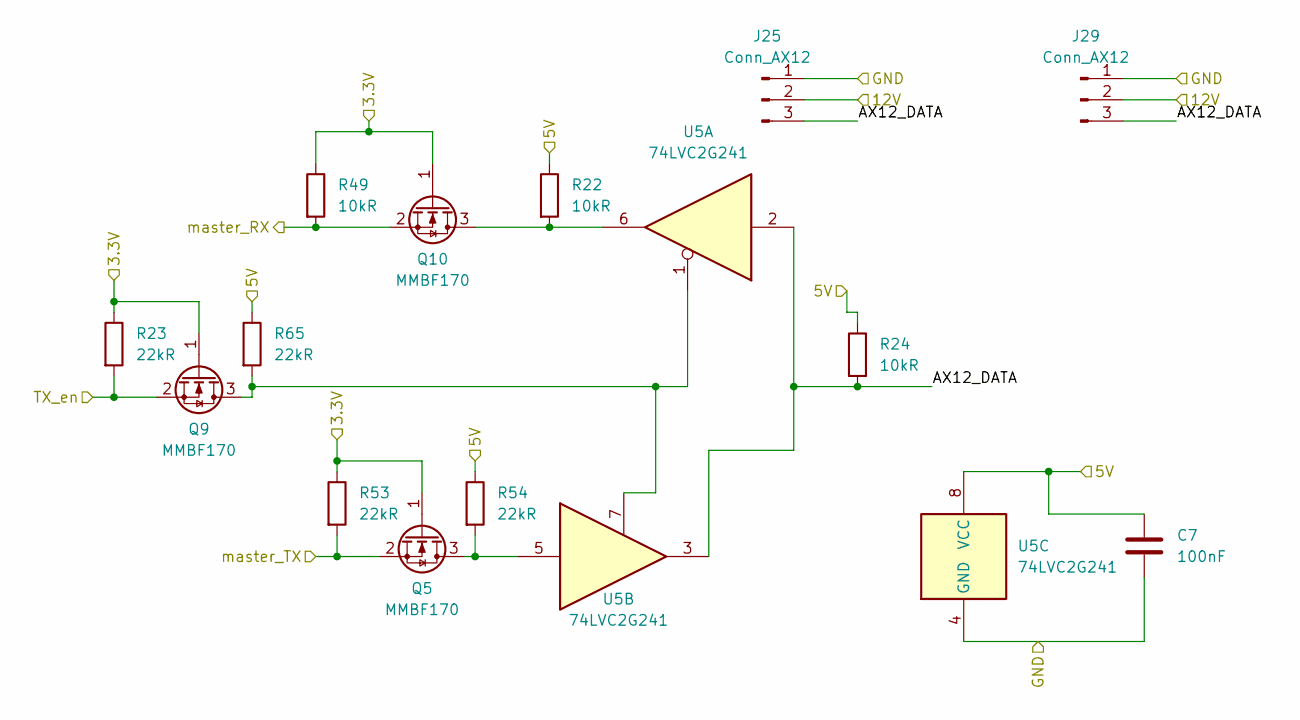
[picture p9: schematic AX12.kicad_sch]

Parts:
C7: 100nF; C_0603_1608Metric; LCSC# C14663
J25, J29: Conn_AX12; JST_XH_B3B-XH-A_1x03_P2.50mm_Vertical; LCSC# C144394
Q5, Q9, Q10: MMBF170; SOT-23; LCSC# C28871
R22, R24, R49: 10kR; R_0603_1608Metric; LCSC# C2930027
R23, R53, R54, R65: 22kR; R_0603_1608Metric; LCSC# C2907128
U5: 74LVC2G241; VSSOP-8_2.4x2.1mm_P0.5mm; LCSC# C10430

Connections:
3.3V: Q5.1 (G), Q9.1 (G), Q10.1 (G), R23.1, R49.1, R53.1; also elsewhere on the board
5V: C7.1, R22.1, R24.1, R54.1, R65.1, U5.8 (VCC); also elsewhere on the board
/AX12_con/AX12_DATA: J25.3, J29.3, R24.2, U5.2, U5.3
AX12_master_RX: Q10.2 (S), R49.2; also elsewhere on the board
AX12_master_TX: Q5.2 (S), R53.2; also elsewhere on the board
AX12_tx_en: Q9.2 (S), R23.2; also elsewhere on the board
BATT_12V: J25.2, J29.2; also elsewhere on the board
GND: C7.2, J25.1, J29.1, U5.4 (GND); also elsewhere on the board
unnamed: Q5.3 (D), R54.2, U5.5
unnamed: Q9.3 (D), R65.2, U5.1, U5.7
unnamed: Q10.3 (D), R22.2, U5.6

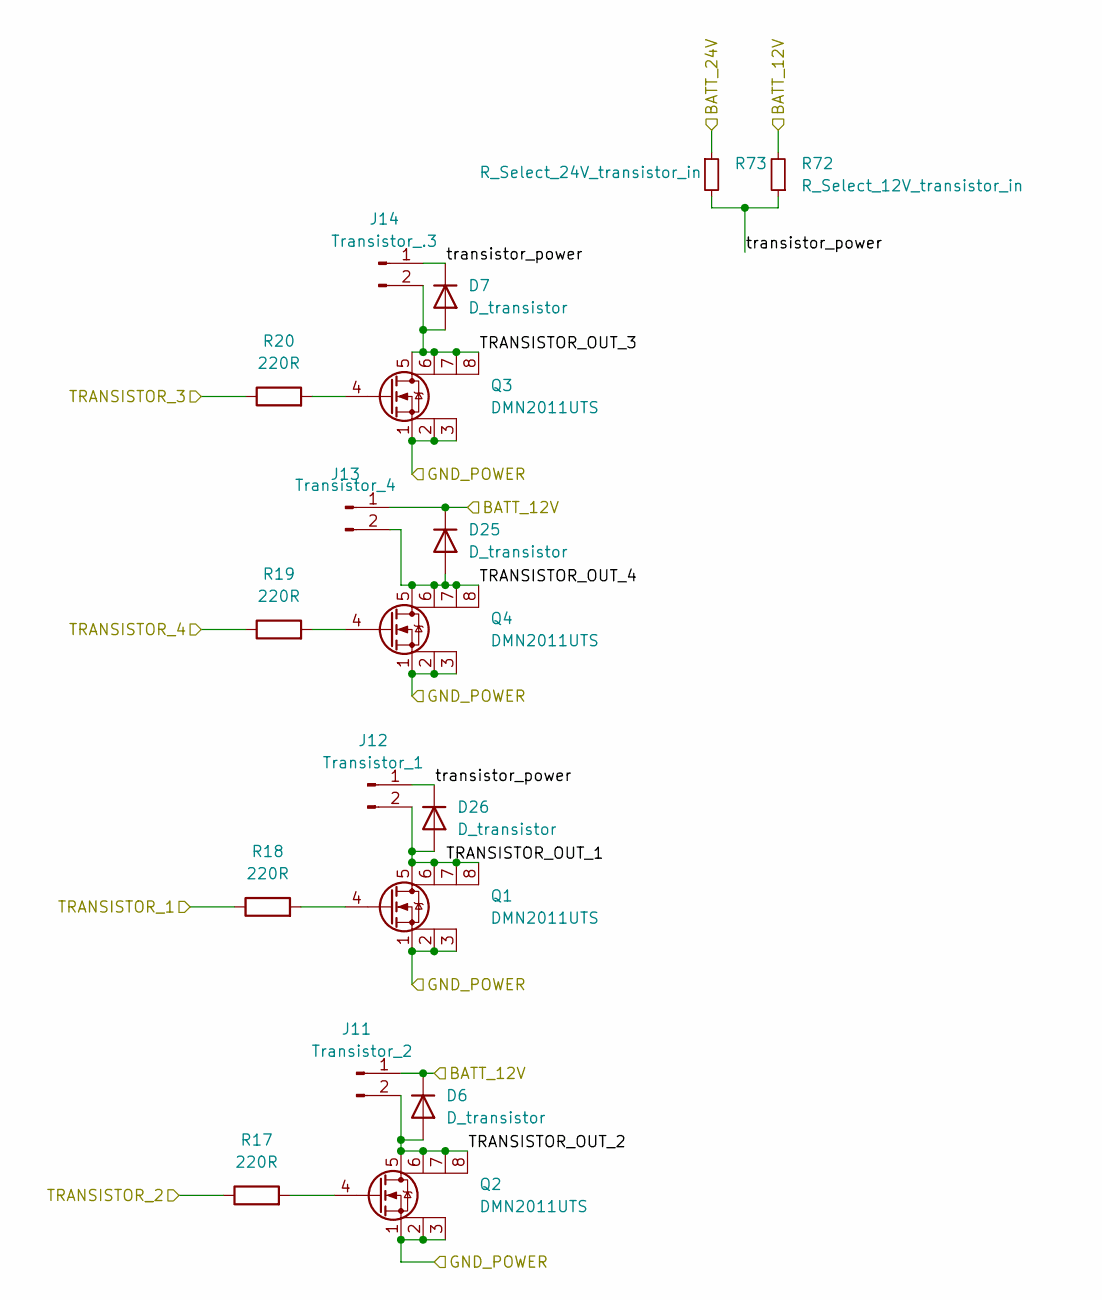
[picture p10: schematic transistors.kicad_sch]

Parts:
D6, D7, D25, D26: D_transistor; D_SOD-123; LCSC# C908230
J11: Transistor_2; JST_XH_B2B-XH-A_1x02_P2.50mm_Vertical; LCSC# C158012
J12: Transistor_1; JST_XH_B2B-XH-A_1x02_P2.50mm_Vertical; LCSC# C158012
J13: Transistor_4; JST_XH_B2B-XH-A_1x02_P2.50mm_Vertical; LCSC# C158012
J14: Transistor_.3; JST_XH_B2B-XH-A_1x02_P2.50mm_Vertical; LCSC# C158012
Q1, Q2, Q3, Q4: DMN2011UTS; TSSOP-8_4.4x3mm_P0.65mm; LCSC# C5245271
R17, R18, R19, R20: 220R; R_0603_1608Metric; LCSC# C2907127
R72: R_Select_12V_transistor_in; R_1206_3216Metric; LCSC# C2907406
R73: R_Select_24V_transistor_in; R_1206_3216Metric; LCSC# C2907406

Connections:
/transistors_outputs/TRANSISTOR_OUT_1: D26.2 (A), J12.2, Q1.5 (D), Q1.6 (D), Q1.7 (D), Q1.8 (D)
/transistors_outputs/TRANSISTOR_OUT_2: D6.2 (A), J11.2, Q2.5 (D), Q2.6 (D), Q2.7 (D), Q2.8 (D)
/transistors_outputs/TRANSISTOR_OUT_3: D7.2 (A), J14.2, Q3.5 (D), Q3.6 (D), Q3.7 (D), Q3.8 (D)
/transistors_outputs/TRANSISTOR_OUT_4: D25.2 (A), J13.2, Q4.5 (D), Q4.6 (D), Q4.7 (D), Q4.8 (D)
/transistors_outputs/transistor_power: D7.1 (K), D26.1 (K), J12.1, J14.1, R72.1, R73.2
BATT_12V: D6.1 (K), D25.1 (K), J11.1, J13.1, R72.2; also elsewhere on the board
BATT_24V_power: R73.1; also elsewhere on the board
GND: Q1.1 (S), Q1.2 (S), Q1.3 (S), Q2.1 (S), Q2.2 (S), Q2.3 (S), Q3.1 (S), Q3.2 (S), Q3.3 (S), Q4.1 (S), Q4.2 (S), Q4.3 (S); also elsewhere on the board
unnamed: Q1.4 (G), R18.2
unnamed: Q2.4 (G), R17.2
unnamed: Q3.4 (G), R20.2
unnamed: Q4.4 (G), R19.2
TRANSISTOR_1: R18.1; also elsewhere on the board
TRANSISTOR_2: R17.1; also elsewhere on the board
TRANSISTOR_3: R20.1; also elsewhere on the board
TRANSISTOR_4: R19.1; also elsewhere on the board

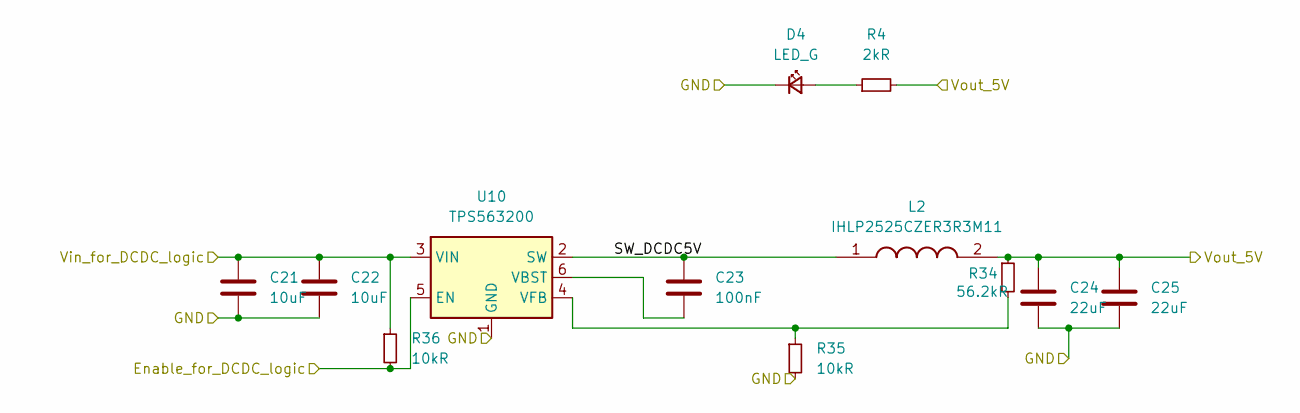
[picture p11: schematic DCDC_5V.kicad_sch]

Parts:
C21, C22: 10uF; C_0805_2012Metric; LCSC# C440198
C23: 100nF; C_0603_1608Metric; LCSC# C14663
C24, C25: 22uF; LED_0805_2012Metric; LCSC# C29277
D4: LED_G; LED_0805_2012Metric; LCSC# C965815
L2: IHLP2525CZER3R3M11; INDPM6965X300N; LCSC# C845025
R4: 2kR; R_0603_1608Metric; LCSC# C2907137
R34: 56.2kR; C_0603_1608Metric; LCSC# C2930117
R35, R36: 10kR; R_0603_1608Metric; LCSC# C2930027
U10: TPS563200; SOT-23-6; LCSC# C97253

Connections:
5V: C24.1, C25.1, L2.2, R4.2, R34.1; also elsewhere on the board
/DCDC_5V/Enable_for_DCDC_logic: R36.2, U10.5 (EN)
/DCDC_5V/SW_DCDC5V: C23.1, L2.1, U10.2 (SW)
BATT_12V_elec: C21.1, C22.1, R36.1, U10.3 (VIN); also elsewhere on the board
GND: C21.2, C22.2, C24.2, C25.2, D4.1 (K), R35.2, U10.1 (GND); also elsewhere on the board
unnamed: D4.2 (A), R4.1
unnamed: C23.2, U10.6 (VBST)
unnamed: R34.2, R35.1, U10.4 (VFB)

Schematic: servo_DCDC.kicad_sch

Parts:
C13: 2.2uF; C_0805_2012Metric; LCSC# C19110
C14: 470nF; C_0603_1608Metric; LCSC# C2905413
C15: 68pF; C_0603_1608Metric; LCSC# C62782
C16, C17, C30: 47uF; C_1210_3225Metric; LCSC# C5440143
C18: 10nF (12V) - 15nF (24V); C_0603_1608Metric; LCSC# C296713
C19, C20: 10uF; C_0805_2012Metric; LCSC# C440198
L1: XAL6030-182MEB; IND_XAL6030-122MEC; PARTREV 11/02/18; LCSC# C19191693
Q7: CSD17307Q5A; TDSON-8-1; LCSC# C78118
Q8: CSD17579Q5A; TDSON-8-1; LCSC# C2760461
R1: 1.74kR; C_0603_1608Metric; LCSC# C2930053
R31: 52.3kR (12V) - 42.2kR (24V); R_0603_1608Metric; LCSC# C23167
R32: 88.7kR; C_0603_1608Metric; LCSC# C2999456
R33: 9.76kR; C_0603_1608Metric; LCSC# C2933269
U9: LM3150MH; Texas_HTSSOP-14-1EP_4.4x5mm_P0.65mm_EP3.4x5mm_Mask3.155x3.2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; LCSC# C1519420

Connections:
/ServoDCDC/SW: C14.1, L1.1, Q7.1 (S), Q7.2 (S), Q7.3 (S), Q8.5 (D), R1.2, U9.10 (SW)
/ServoDCDC/VIN: C19.2, C20.2, Q7.5 (D), R31.1, U9.2 (VIN); also elsewhere on the board
/ServoDCDC/VOUT: C15.2, C16.1, C17.1, C30.1, L1.2, R32.2; also elsewhere on the board
ENABLE_SERVO_POWER_1: U9.3 (EN); also elsewhere on the board
GND: C13.1, C16.2, C17.2, C18.1, C19.1, C20.1, C30.2, Q8.1 (S), Q8.2 (S), Q8.3 (S), R33.1, U9.5 (SGND), U9.9 (SGND), U9.14 (PGND), U9.15 (SGND); also elsewhere on the board
unnamed: Q7.4 (G), U9.11 (HG)
unnamed: Q8.4 (G), U9.13 (LG)
unnamed: C14.2, U9.12 (BST)
unnamed: C15.1, R32.1, R33.2, U9.4 (FB)
unnamed: R1.1, U9.8 (ILIM)
unnamed: R31.2, U9.7 (RON)
unnamed: C18.2, U9.6 (SS)
unnamed: C13.2, U9.1 (VCC)

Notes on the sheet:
24V input: L2 XAL6030-182MEB C19191693 (même empreinte) haut CSD18504Q5A C78118 (même empreinte) bas CSD18563Q5A C2760461 (même empreinte)
12V input: L2 XAL6030-122MEC C19191689 (même empreinte) haut CSD17307Q5A C22367097 (même empreinte) bas CSD17579Q5A CSD17579Q5A (même empreinte)

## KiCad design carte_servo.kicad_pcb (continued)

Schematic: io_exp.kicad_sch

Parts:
C34: 2.2uF; C_0805_2012Metric; LCSC# C19110
J4, J26, J27, J28: Conn_01x03; JST_XH_B3B-XH-A_1x03_P2.50mm_Vertical; LCSC# C144394
R40, R43, R45, R47: 3.3V; R_0603_1608Metric
R41, R42, R44, R46: 12V; R_0603_1608Metric
R50: 10kR; R_0603_1608Metric; LCSC# C2930027
R55, R58, R60, R62: 22kR; R_0603_1608Metric; LCSC# C2907128
R56, R57, R59, R61: 56.2kR; R_0603_1608Metric; LCSC# C2930117
U11: PCF8574ATS; SSOP-20_4.4x6.5mm_P0.65mm; LCSC# C2803277

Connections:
3.3V: C34.1, R40.1, R43.1, R45.1, R47.1, R50.1, U11.5 (VDD); also elsewhere on the board
/IO_expander/SIG_0: R55.1, R56.2, U11.10 (P0)
/IO_expander/SIG_1: R57.1, R58.1, U11.11 (P1)
/IO_expander/SIG_2: R59.2, R60.1, U11.12 (P2)
/IO_expander/SIG_3: R61.2, R62.1, U11.14 (P3)
BATT_12V_elec: R41.1, R42.1, R44.1, R46.1; also elsewhere on the board
GND: C34.2, J4.1, J26.1, J27.1, J28.1, R55.2, R58.2, R60.2, R62.2, U11.6 (A0), U11.7 (A1), U11.9 (A2), U11.15 (VSS); also elsewhere on the board
I2C_extra_2: U11.20 (P7); also elsewhere on the board
unnamed: J4.2, R40.2, R41.2
unnamed: J4.3, R56.1
unnamed: J26.2, R42.2, R43.2
unnamed: J26.3, R57.2
unnamed: J27.2, R44.2, R45.2
unnamed: J27.3, R59.1
unnamed: J28.2, R46.2, R47.2
unnamed: J28.3, R61.1
unnamed: R50.2, U11.1 (~INT)
SCL: U11.2 (SCL); also elsewhere on the board
SDA: U11.4 (SDA); also elsewhere on the board
TRANSISTOR_1: U11.16 (P4); also elsewhere on the board
TRANSISTOR_3: U11.17 (P5); also elsewhere on the board
TRANSISTOR_4: U11.19 (P6); also elsewhere on the board

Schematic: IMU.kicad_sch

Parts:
C36: 2.2nF; C_0603_1608Metric; LCSC# C14663
C37, C38, C39: 100nF; C_0603_1608Metric; LCSC# C14663
U12: MPU-6050; InvenSense_QFN-24_4x4mm_P0.5mm

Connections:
3.3V: C37.1, C39.1, U12.8 (VLOGIC), U12.13 (VDD); also elsewhere on the board
GND: C36.2, C37.2, C38.1, C39.2, U12.1 (CLKIN), U12.9 (AD0), U12.11 (FSYNC), U12.18 (GND); also elsewhere on the board
unnamed: C36.1, U12.20 (CPOUT)
unnamed: C38.2, U12.10 (REGOUT)
SCL: U12.23 (SCL); also elsewhere on the board
SDA: U12.24 (SDA); also elsewhere on the board

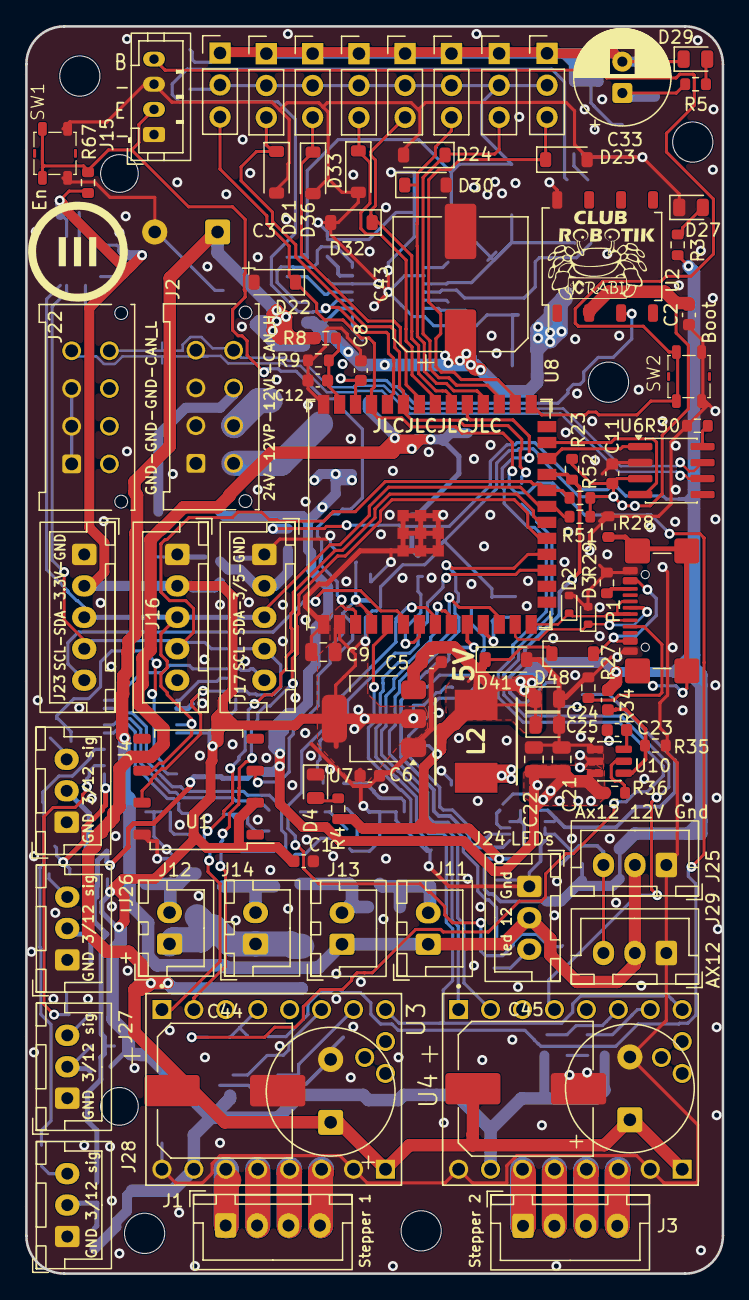
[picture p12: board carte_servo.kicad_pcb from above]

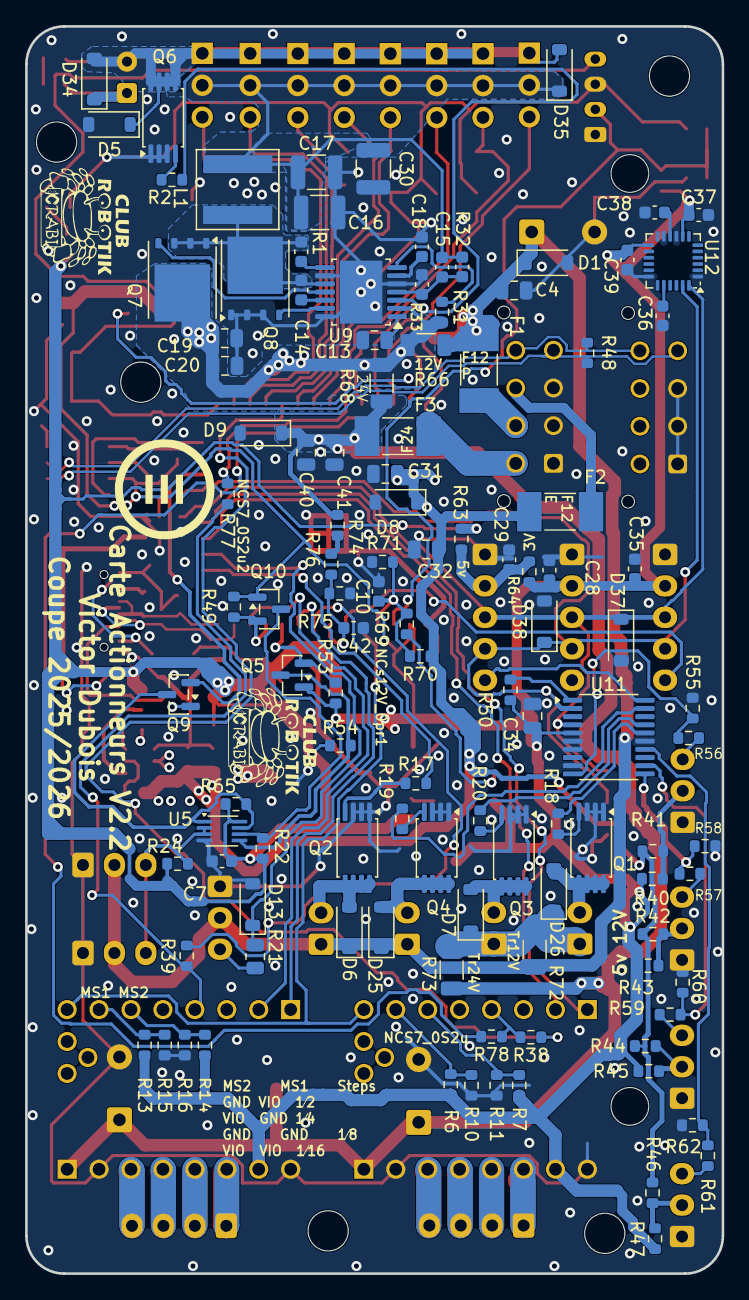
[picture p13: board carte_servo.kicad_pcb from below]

Board: 4 copper layers, 55.4 x 99.2 mm, 213 parts (114 on the bottom side), 120 nets.

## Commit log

2022-04-10 version without mega I2C pins
    [carte_servo.kicad_pcb, carte_servo.kicad_sch, servos.kicad_sch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]
2022-04-15 use mega I2C port
    [carte_servo.kicad_pcb, carte_servo.kicad_sch]
2022-04-17 add 2 servos + possibility to measure Vbatt
    [carte_servo.kicad_pcb, carte_servo.kicad_sch, servos.kicad_sch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]
2022-04-20 JST_PH=>JST_XH. Version envoyee en fab
    [carte_servo.kicad_pcb, carte_servo.kicad_sch, transistors.kicad_sch]
2022-05-12 specify values + BOM
    [BOM.ods, carte_servo.kicad_sch, servos.kicad_sch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]
2022-10-08 [WiP] debut de V2
    [carte_servo.kicad_pcb, carte_servo.kicad_sch, servos.kicad_sch]
2023-10-04 fix driving servo power (NMOS on GND) + fix 12V connector position
    [carte_servo.kicad_pcb, carte_servo.kicad_sch, servos.kicad_sch]
2023-10-13 add AX12 connector + LED strip connector + libraries todo : add 12V connectors, change stepper connectors
    [AX12.kicad_sch, TMC2208_SILENTSTEPSTICK.step, carte_servo.kicad_pcb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]
2023-10-26 add second AX12 connector + change stepper connectors + add 12V connector. Todo : add SPI for RFID
    [AX12.kicad_sch, carte_servo.kicad_pcb, carte_servo.kicad_sch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]
2023-10-29 Add SPI connector + route control pins (LEDs, AX12)
    [AX12.kicad_sch, carte_servo.kicad_pcb, carte_servo.kicad_sch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]
2023-10-30 add zeners for new connections
    [carte_servo.kicad_pcb, carte_servo.kicad_sch, stepper_driver.kicad_sch]
2023-10-30 4 layers
    [carte_servo.kicad_pcb]
2023-10-30 Change to SOD-123 diodes
    [carte_servo.kicad_pcb, carte_servo.kicad_sch]
2023-11-02 route STEP and DIR for both stepper motors
    [AX12.kicad_sch, carte_servo.kicad_sch, stepper_driver.kicad_sch]
2025-01-03 WiP start switching to an ESP32
    [AX12.kicad_sch, carte_servo.kicad_pcb, carte_servo.kicad_sch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]
2025-01-29 start adapting to new connectors
    [carte_servo.kicad_sch]
2025-01-29 remove intra-board zeners
    [AX12.kicad_sch, diodes.kicad_sch]
2025-01-29 start placing components from scratch
    [carte_servo.kicad_pcb]
2025-02-02 add DCDC 6V
    [carte_servo.kicad_pcb, carte_servo.kicad_sch, servo_DCDC.kicad_sch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]
2025-02-08 small stuff
    [AX12.kicad_sch, carte_servo.kicad_pcb, carte_servo.kicad_sch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]
2025-02-08 add DCDC 5V
    [DCDC_5V.kicad_sch, carte_servo.kicad_pcb, carte_servo.kicad_sch]
2025-02-08 add ESD diodes for USB
    [carte_servo.kicad_pcb, carte_servo.kicad_sch]
2025-02-09 fix warnings + separate enable for Steppers
    [DCDC_5V.kicad_sch, carte_servo.kicad_pcb, carte_servo.kicad_sch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]
2025-02-09 change fuse + start servo order + routing
    [carte_servo.kicad_pcb, carte_servo.kicad_sch, servos.kicad_sch]
2025-02-09 continue routing
    [carte_servo.kicad_pcb]
2025-02-10 continue routing. Shorter SW_6V and 12V from connector to big capa
    [carte_servo.kicad_pcb]
2025-02-15 basic routing
    [carte_servo.kicad_pcb, carte_servo.kicad_sch]
2025-02-15 widen 12V/5V
    [carte_servo.kicad_pcb, carte_servo.kicad_sch]
2025-02-16 add vias and stuff
    [carte_servo.kicad_pcb]
2025-02-16 (fields_autoplaced yes)
    [AX12.kicad_sch, DCDC_5V.kicad_sch, servo_DCDC.kicad_sch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]
2025-02-16 add mounting holes
    [carte_servo.kicad_pcb, carte_servo.kicad_sch]
2025-02-16 add power status LEDs
    [DCDC_5V.kicad_sch, carte_servo.kicad_pcb, servos.kicad_sch]
2025-02-16 12V logic for ESP32 + add legends + fine tune
    [DCDC_5V.kicad_sch, carte_servo.kicad_pcb, carte_servo.kicad_sch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]
2025-02-22 fix warnings + add internal layers + add Uart to steppers (TX only
    [AX12.kicad_sch, carte_servo.kicad_pcb, carte_servo.kicad_sch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]
2025-02-22 export bom as CSV
    [carte_servo.csv, carte_servo.kicad_pcb, carte_servo.kicad_sch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]
2025-02-22 add capa for servos
    [carte_servo.kicad_pcb, carte_servo.kicad_sch, servos.kicad_sch]
2025-02-22 fix warnings, change USB-C and button
    [carte_servo.kicad_pcb, carte_servo.kicad_sch]
2025-02-22 fine tuning
    [carte_servo.kicad_pcb, carte_servo.kicad_sch]
2025-02-28 fine-tuning (move 5V away from SW_6V)
    [carte_servo.kicad_pcb]
2025-02-28 add registration holes
    [AX12.kicad_sch, carte_servo.kicad_pcb, carte_servo.kicad_sch]
2025-03-01 add edge of stencil
    [carte_servo.kicad_pcb]
2025-03-02 add registration holes to paste layers
    [carte_servo.kicad_pcb]
2025-03-02 update BOM
    [carte_servo.csv, servo_DCDC.kicad_sch]
2025-03-02 -10% for stencil
    [carte_servo.kicad_pcb]
2025-03-02 fix DCDC5V schematic
    [DCDC_5V.kicad_sch, carte_servo.kicad_pcb]
2025-03-02 SW_5V is internal layer
    [carte_servo.kicad_pcb]
2025-03-06 better routing
    [carte_servo.kicad_pcb]
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2025-03-07 finish routing IO_exp + some fine-tuning
    [carte_servo.kicad_pcb]
2025-03-09 Add BOM
    Add LCSC reference and correct few footprint acording bom
    [AX12.kicad_sch, DCDC_5V.kicad_sch, carte_servo.csv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]
2025-03-09 fix 1 error + warnings, mainly silkscreen
    [carte_servo.kicad_pcb]
2025-03-09 improve DCDC current routing
    [carte_servo.kicad_pcb]
2025-04-21 fix 3.3V/5V compatibility + add 120Ohms + add I2C pullups
    [AX12.kicad_sch, carte_servo.kicad_pcb, carte_servo.kicad_sch]
2025-04-21 [WiP] start add MPU6050
    [carte_servo.kicad_pcb, carte_servo.kicad_sch]
2025-04-22 Go to 3.3V + fix io_exp + routing
    [AX12.kicad_sch, carte_servo.kicad_pcb, carte_servo.kicad_sch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]
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2025-05-12 add 3.3V/5V conversion on AX12 RX/TX enable
    [AX12.kicad_sch, carte_servo.kicad_pcb]
2025-06-27 fix previous commit
    [carte_servo.kicad_pcb]
2025-06-27 Huge cleanup of the schematic
    [IMU.kicad_sch, USB_conn.kicad_sch, carte_servo.kicad_pcb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]
2025-08-24 prepare DCDC 24V compatibility + add reset/boot connector
    [carte_servo.kicad_pcb, carte_servo.kicad_sch, servo_DCDC.kicad_sch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]
2025-08-27 fix error + add fuse/resistor choice servo DCDC vin = 12V or 24V
    [carte_servo.kicad_pcb, carte_servo.kicad_sch, stepper_driver.kicad_sch]
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2025-10-27 fix AX12 RX: add proper 3.3V/5V level shifter
    [AX12.kicad_sch, carte_servo.kicad_pcb, carte_servo.kicad_sch]
2025-10-27 add missing pullup on IO_exp INT
    [carte_servo.kicad_pcb, io_exp.kicad_sch]
2025-10-27 add 12V elec measure
    [carte_servo.kicad_pcb, carte_servo.kicad_sch]
2025-10-28 add possibility to have 2 of the transistor outputs to use either 12V or 24V
    [carte_servo.kicad_pcb, carte_servo.kicad_sch, transistors.kicad_sch]
2025-10-28 add 24V monitoring, move transistor4 to IO_exp (former I2C extra 1)
    [carte_servo.kicad_pcb, carte_servo.kicad_sch]
2025-10-29 tuning + add silkscreen
    [carte_servo.kicad_pcb]
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2025-12-30 update to Kicad 9 + small fixes
    [AX12.kicad_sch, DCDC_5V.kicad_sch, IMU.kicad_sch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]
2025-12-30 fix warnings + add big capa on 6V DCDC input
    [carte_servo.kicad_pcb, carte_servo.kicad_sch, diodes.kicad_sch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]
2026-02-05 update BOM + add big capas (do not take DNP into account)
    [AX12.kicad_sch, DCDC_5V.kicad_sch, IMU.kicad_sch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]
2026-02-05 fix DNP (was just for checking what was to be bought)
    [AX12.kicad_sch, DCDC_5V.kicad_sch, IMU.kicad_sch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]
2026-02-05 fix dnp
    [carte_servo.kicad_pcb]
2026-02-06 change capacitor references to support >25V
    [DCDC_5V.kicad_sch, servo_DCDC.kicad_sch]
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2026-06-20 update to Kicad 10 + start fixing warnings
    [AX12.kicad_sch, DCDC_5V.kicad_sch, IMU.kicad_sch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]
2026-06-28 fix diodes on transistors + fix warnings
    [USB_conn.kicad_sch, carte_servo.kicad_pcb, carte_servo.kicad_sch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]
